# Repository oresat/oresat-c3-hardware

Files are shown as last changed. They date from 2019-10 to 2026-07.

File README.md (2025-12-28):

# oresat-c3
## General information
This is the C3 (Command, Communication, and Control) card for OreSat. It acts as the central control point for the entire OreSat project, provides
telemetry to the ground, and receiver commands. It's the "on board computer" (OBC) of the OreSat bus. It has:

- Octavo OSD335x-SM SIP AM335X-based Cortex A8 Microporcessor
- On Semi AX5043-based L Band (1.265 GHz) receiver
- On Semi AX5043-based UHF Band (436.5 MHz) receiver and transmitter with 1W PA.
- Custom radiation tolerant watchdog timer based on the TI TLV1042 comparator.
- 16 GB eMMC flash data storage
- 1 Mbit of FRAM for high reliability state and variable storage
- Supercapacitor-backed up RTC
- Two antenna deployment circuits
- OreSat Power Domain (OPD) control circuitry

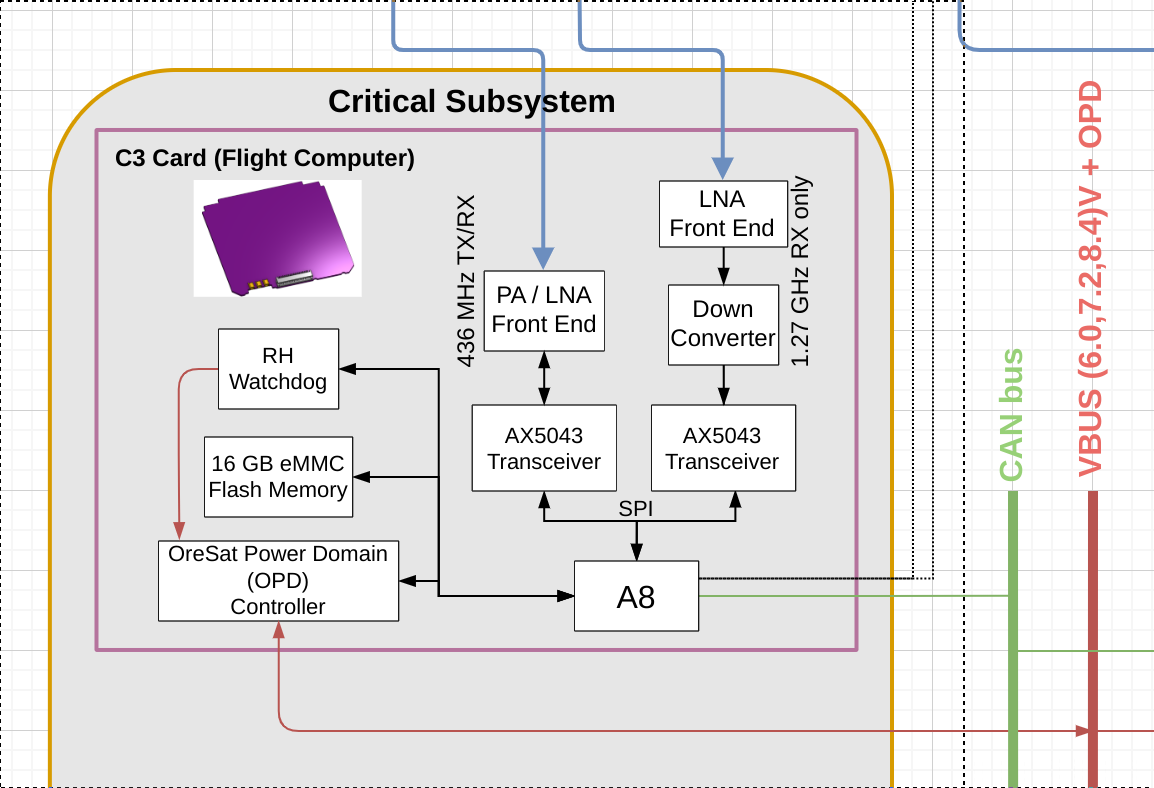
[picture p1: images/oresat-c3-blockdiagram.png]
C3 block digram


Design materials are on Google docs; we'll post links / PDFs soon.

Bill of Materials (BOM) can be found [here](https://docs.google.com/spreadsheets/d/11vG1kWyrAjmbF5QJM-EhXmvQoF6O47japwYlHF802do/edit#gid=1239769296).

## OreSat C3 version 6 (KiCAD)

Fixes for the radio receivers, version 2 backplane pinout, and lots of little tweaks
after our lessons learned on OreSat0. OH, and a COMPLETE REFACTOR since we switched from
the STM32F439 to an Octavo OSD335x-SM and switched from EAGLE to KICAD. Yikes.

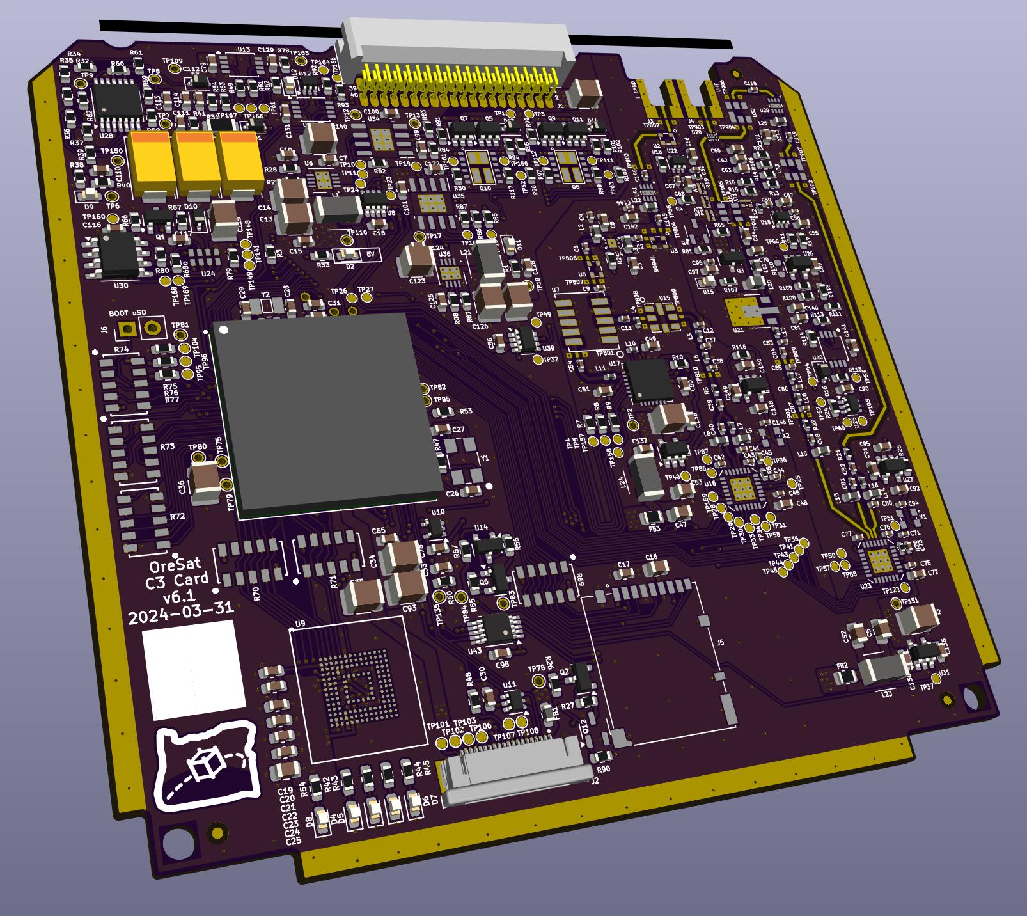
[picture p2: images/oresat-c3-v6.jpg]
C3 version 6 PCBA


### V6 Software

The C3 runs Python code that interacts with the radios, peripherals, and CAN bus. [Here's more information](https://github.com/oresat/oresat-c3-software).

## OreSat C3 version 5 (EAGLE)

C3 V5 flew on Oresat0, Oregon's first satellite! Everything worked great, except for the
radio receivers (L band LNA oscillated, and UHF LNA was turned off in firmware).

### v5 Firmware

The firmware for the C3 card is written in C and runs on top of ChibiOS, a small RTOS.
It is integrated into the [oresat-firmware](https://github.com/oresat/oresat-firmware) repository.
The firmware application for this project is located
[here](https://github.com/oresat/oresat-firmware/tree/c3_capstone/src/f4/app_c3_v1).

## OreSat C3 version 4 (EAGLE)

C3 V4 is our latest version of the C3 card; it's getting ready for flight in 
Q2 2021 in OreSat0. It's got all of the functionality necessary for flight.

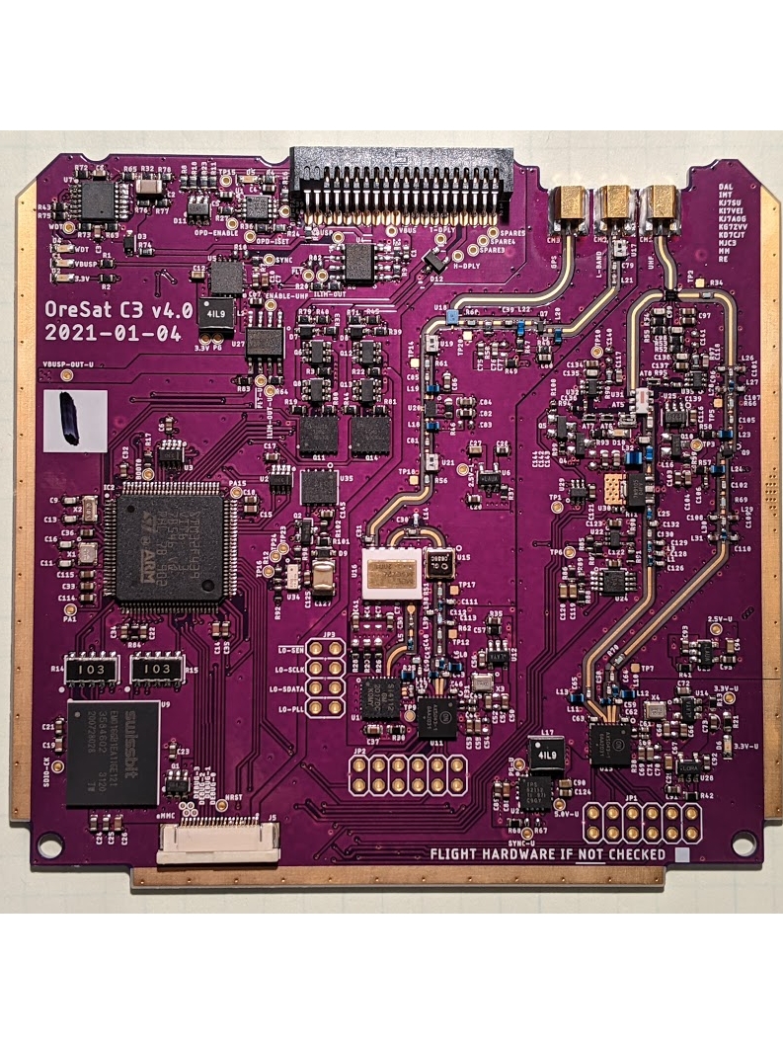
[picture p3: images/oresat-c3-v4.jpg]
C3 version 4 PCBA


## OreSat C3 V3 (2019-2020 ECE Capstone)

The 2018-2019 ECE Capstone brought the card to version 3. It implements an
STM32F446VET6 IC, the full L band receiver with ultistage LNA, and a UHF radio 
with LNA but no PA for transmitting.

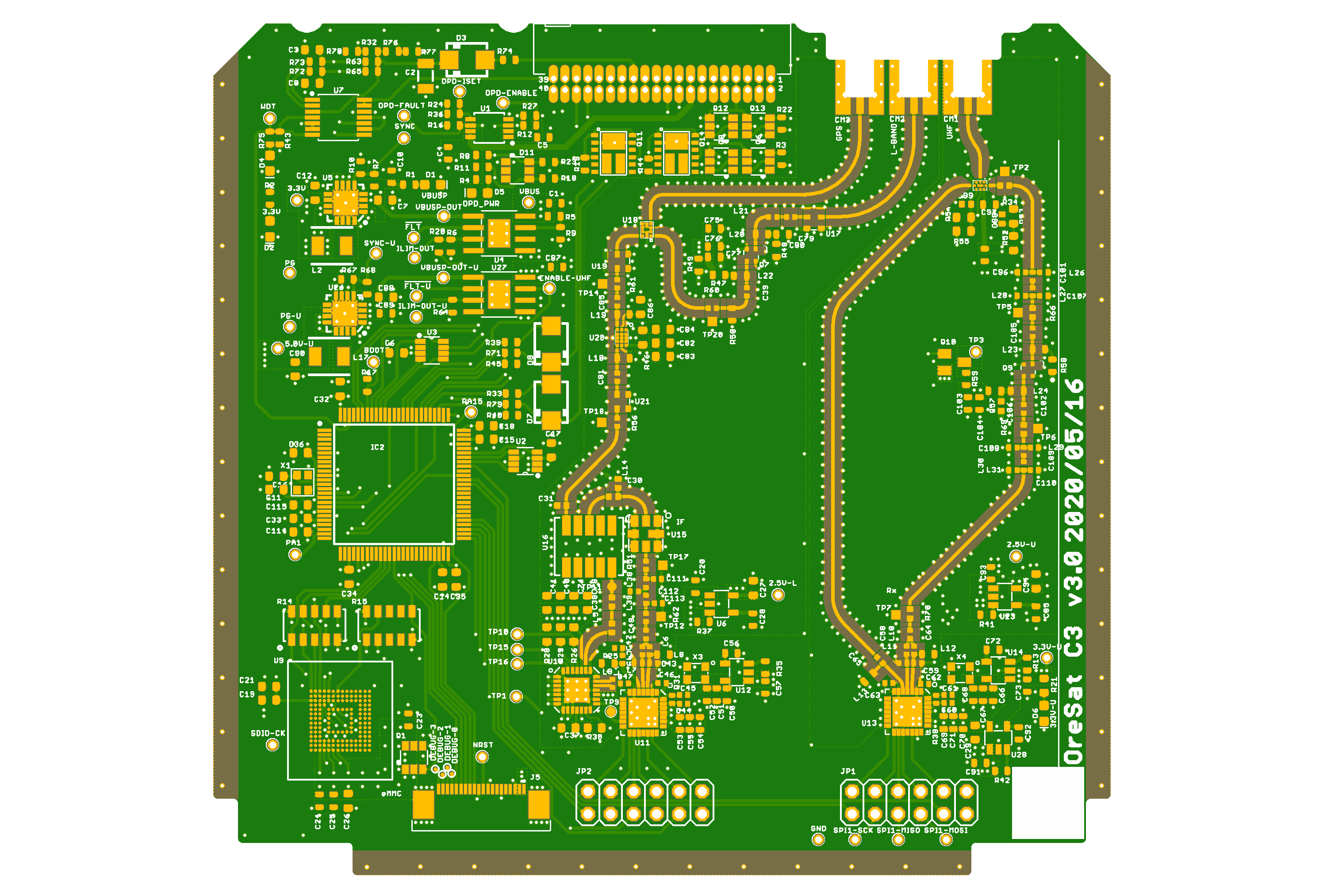
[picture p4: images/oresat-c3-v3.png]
C3 version 3 PCBA


## Breadboard Prototype

Most embedded project starts out as a bunch of development boards strung together;
the C3 is no different! The breadboard prototype for the C3 card implements an
STM32F446RE development board connected to two SPI radios, the OreSat
FlatSat backplane via a CAN transceiver and I2C for the OPD interface,
and a SDIO and SPI connected SD/MMC Card. The breadboard implements
stronger pullups for the I2C lines than the GPIO of the STM32 can
provide. It is currently capable of interfacing with and activating the
OPD connected boards.

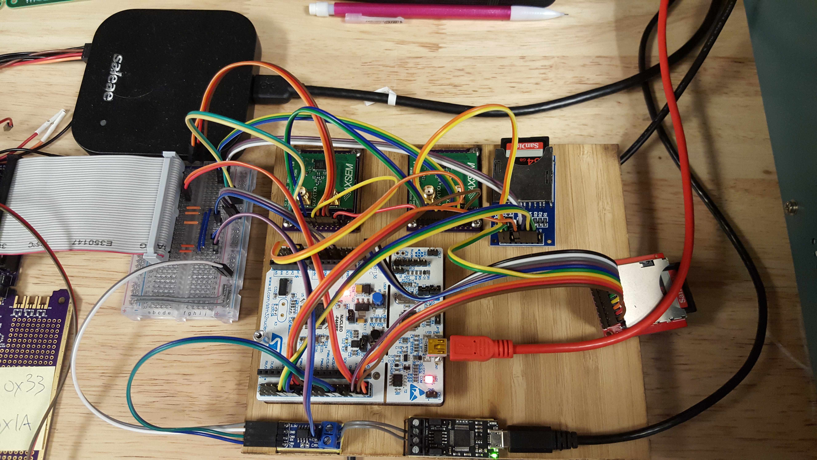
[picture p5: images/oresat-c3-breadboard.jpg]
Breadboard Prototype


## License

All materials in this repo are copyright Portland State Aerospace Society and are licensed under the CERN Open Hardware Licence Version 2 -
Strongly Reciprocal (CERN-OHL-S v2), or any later version. A copy of the license is located in [here](LICENSE.md).

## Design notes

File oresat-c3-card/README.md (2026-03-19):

---
title: "**OreSat C3 Card**"
subtitle: |
  **Fabrication and Assembly Information**\
  For build TIME-STAMP
fontsize: 10pt
geometry:
  - margin=0.5in
toc: true
toc-depth: 2
colorlinks: true
urlcolor: blue
---

\newpage

# About this Board

## Board Description

The C3 ("Command, Control, and Communications") card is the main on-board computer (OBC) / housekeeping unit (HKU) / Command and Data Handling (CDH) subsystem for the open source [OreSat CubeSat system](https://www.oresat.org/). The C3 card:

- Connects to the backplane with a main connector and two RF ports
- Has an L band radio receiver based on the AT86RF215.
- Has a UHF radio transceiver based on the AT86RF215
- Has a radiation tolerant watchdog timer (with a cheap commercial replacement if you're not going to orbit)
- Controls the OreSat Power Domain (OPD), which turns on and off and controls other cards
- Talks to both CAN OreSat CAN busses

## Documentation Links

- C3 hardware Git repository: <https://github.com/oresat/oresat-c3-hardware>
- C3 software Git reposity: <https://github.com/oresat/oresat-c3-software>
- **TODO:** C3 Design Notes + Design Review Notes

## Documentation Files

| Filename | Notes |
| --- | --- |
| README.pdf | This README file |
| PROJECT-NAME-outline.dxf | Board outline (with holes) in DXF format |
| PROJECT-NAME-pcba.step | 3D model of PCBA (with components) |
| PROJECT-NAME-render-bot.jpg | Render of the top of the 3D model |
| PROJECT-NAME-render-bot.jpg | Render of the bottom of the 3D model |
| PROJECT-NAME-schematic.pdf | PDF of board schematics |

## Contact Information

- Website: <https://www.oresat.org/>
- Email: <oresat@pdx.edu>
- Instagram: @pdxaerospace

## Board Renders

Render of the top of the 3D model
Render of the bottom of the 3D model

\newpage

# Printed Circuit Board (PCB) Fabrication Information

## Board Info

- 4 layer board
- Bounding box is 99.8 x 94.6 mm (3.93 x 3.72 in)
- Board thickness is 1.59 mm (0.063 inch)
- **Important:** See Materials and Stack Up sections below

## Board Requirements

- Design Rules
    - Minimum Trace / Space design rules
       - Outer layers: 0.127 mm (5.0 mil) / 0.127 mm (5.0 mil)
       - Inner layers: 0.127 mm (5.0 mil) / 0.127 mm (5.0 mil)
    - Outer dimension router tolerance: +/- 0.254 mm (10.0 mil)
    - Hole placement tolerance: +/- 0.075 mm (3.0 mil)
    - Inner tab routed slot tolerance: +/- 0.254 mm (10.0 mil)
- Drills
   - Drill Positional Tolerance: 0.051 mm (2.0 mil)
   - Drill Size tolerance: +/- 0.064 mm (2.5 mil)
- Plated/Un-plated holes
  - There are 6 un-plated (NPT) holes
  - There are 1477 plated through (PTH) holes
  - PTH minimum diameter: 0.254 mm (10 mil)
  - PTH minimum annulus: 0.102 mm (4 mil) radius
- Outline/Routing
  - Requires a 1.0 mm or smaller diameter routing bit
- Slots
  - There are no slots.
- Cutouts
  - There are no cutouts
- There are 3 fiducials on the top layer.
- Panel tabs ("mouse bites")
   - Card edges must be smooth; no mouse bites or other intrusions into the card outline.
   - If external mouse bites are required, minimize and customer will remove by hand before assembly.
- If not otherwise specified, build to IPC 6012 Class 2 or better.

## Materials

- Controlled impedance
   - The stackup is critical for the performance of high speed signals on this board.
   - As long as the stackup is controlled, the board is not considered controlled impedance.
- Isola FR408HR or material with equivalent Dk.
- Board Surface treatment should be ENIG, althogh immersion Silver is acceptable.
- White silkscreen on top and bottom surface
- Taiyo PSR-4000 or equivalent soldermask on top and bottom, no requirements for color.

## Stack Up

| Layer | Thickness | Notes |
|---|---|---|
| Top Copper | 0.043 mm /  1.7 mil |  Layer 1 foil, 1 oz Cu after plating |
| prepreg | 0.200 mm /  7.9 mil |  Prepreg - Isola FR408HR 2113 |
| Layer 2 | 0.018 mm /  0.7 mil |  Layer 2 foil, 0.5 oz Cu |
| Core | 0.991 mm / 39 mil |  Core Isola FR408HR |
| Layer 3 | 0.018 mm /  0.7 mil |  Layer 3 foil, 0.5 oz Cu |
| prepreg | 0.200 mm /  7.9 mil |  Prepreg - Isola FR408HR 2113 |
| Bottom Copper | 0.043 mm /  1.7 mil |  Layer 4 foil, 1 oz copper after plating |
| **Total Stackup** | **1.588 mm / 62.5 mil** | |

## Array / Panel Information

- Coordinate with Contract Manufacturer (CM) for optimal size of this panel.
- If no feedback from CM, then produce single boards (no panel).

## Fabrication Files

### IPC-2581 File

| Filename | Notes |
| --- | --- |
| PROJECT-NAME-ipc2581.xml | IPC-2581 board information file |

### Legacy PCB Files

| Filename | Notes |
| ---| --- |
| PROJECT-NAME-Edge_Cuts.gbr | RS274X file for the dimension (outline) layer |
| PROJECT-NAME-F_Silkscreen.gbr | RS274X file for the top silkscreen |
| PROJECT-NAME-F_Mask.gbr | RS274X file for the top soldermask |
| PROJECT-NAME-F_Cu.gbr | RS274X file for the top copper layer |
| PROJECT-NAME-In1_Cu.gbr | RS274X file for the layer 2 copper |
| PROJECT-NAME-In2_Cu.gbr | RS274X file for the layer 3 copper |
| PROJECT-NAME-B_Cu.gbr | RS274X file for the bottom copper layer |
| PROJECT-NAME-B_Mask.gbr | RS274X file for the bottom soldermask |
| PROJECT-NAME-B_Silkscreen.gbr | RS274X file for the bottom silkscreen |
| PROJECT-NAME-NPTH.drl | Excellon file for non-plated through holes |
| PROJECT-NAME-PTH.drl | Excellon file for plated through holes | 

\newpage

# Printed Circuit Board Assembly (PCBA) Information

## Assembly Info

- All components are on the top side of the board.
- This PCBA is mostly surface mount (SMT) with a few (THT) components.

## Assembly Requirements

- Assemble to IPC Class 2 or better
- Bake components that are not moisture sealed to appropriate levels as required.
- Solder paste MUST be leaded.
- Aqueous flux and wash strongly preferred.
   - Clean to NASA Standard "Visibly Clean (VC)": No particles or residues are visible to the naked eye.
- No conformal coating.
- Ship in antistatic protective bag

## Component Specific Assembly Information

- SMPM connectors (J3, J4) should be hand-added (there is no solder paste for their footprints).
- U1 and U28 are extremely expensive ($75 and $150 ea, respectively).
- U15 and U21 are EOL and will be supplied in cut tape form.

## Assembly Files

### IPC-2581 File

| Filename | Notes |
| --- | --- |
| PROJECT-NAME-ipc2581.xml | IPC-2581 board information file |

### Bill of Materials (BOM)

| Filename | Description |
| --- | --- |
| PROJECT-NAME-bom.csv | BOM in Comma Separated Variable format |

### Solder Paste Stencils

| Filename | Notes |
| --- | --- |
| PROJECT-NAME-B_Paste.gbr | RS274X file for top/front solder paste stencil |
| PROJECT-NAME-F_Paste.gbr | RS274X file for bottom/back solder paste stencil |

### Mounting/Placement Location

| Filename | Description |
| --- | --- |
| PROJECT-NAME-3u.pos | Pick and place locations for components |

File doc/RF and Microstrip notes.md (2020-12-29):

We use OSH Park 4 layer PCB. 50 ohm line on this is 0.38 mm, as we determined by calculation and by measurement.

Decided to move RF net clearance to 0.75 mm which is ~ 4x the dielectric thickness of 0.17 mm. Better than minimum of 3 and worse than the 5 some people say.

The 0.75 mm clearance means that the total RF "width" of the strip and pulled back ground plane is 0.75 * 2 + 0.38 mm = 1.88 mm.

The TSTOP on the RF traces is 1.6 wide, which protects the ground copper with 0.18 mm of coverage on both sides.

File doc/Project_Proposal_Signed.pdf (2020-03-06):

# OreSat Command, Control, and Communication (C3) Card: Project Requirements and Plan

A 2019-2020 ECE capstone project sponsored by the Portland State Aerospace Society

Mikhail Mayers, Robin Ekeya, Marcus Chalona, Miles Simpson, Ian Taylor

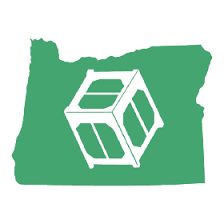
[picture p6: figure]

## Table of Contents

Executive Summary | 3
Project motivation | 3
Product Design Specification | 4
Concept of operations | 4
Stakeholders | 4
Requirements | 5
Design Specifications | 5
Deliverables | 6
Initial Product Design | 7
Oresat C3 Board: Level 0 | 8
Oresat C3 Board: Level 1 | 9
Verification Plans | 11
Project Management Plan | 11
Timeline, with milestones | 11
Budget and Resources | 11
Team and development process | 11

### Executive Summary

Our project’s goal is to deliver a flight ready Command, Control, and Communication (C3) card for OreSat. OreSat (http://cubesat.org/) is Oregon's first satellite. It is an open source 2U CubeSat (https://en.wikipedia.org/wiki/CubeSat) being developed by the Portland State Aerospace Society (PSAS) with a target hand off date to NASA in winter 2021. The C3 card is the "system controller" for the satellite, it oversees the critical, attitude determination/control and mission subsystems.

The C3 card has the radios that link the CubeSat to the mission control on the ground. Once the CubeSat is released from the ISS, the C3 will be responsible for broadcasting a radio beacon so that the ground station can make initial contact and uniquely identify it in space. The C3 is also the heart of OreSat’s radiation tolerance having the single rad-hard part in the satellite.

### Project motivation

OreSat has a modular card-cage system that holds up to 20 cards. On these cards are: the critical subsystems (solar modules, batteries, and telemetry and telecommand radio systems), the attitude determination and control subsystems (IMU, GPS, Star Tracker, Reaction Wheels and Magnetorquers), and finally the mission subsystems (OreSat Live and the Cirrus Flux Camera). The C3 card ties all of these cards together into a functional satellite.

One of the challenges with developing a flight ready CubeSat is the harsh operating environment presented by space. Besides the stresses of vibration and extreme temperatures, ionizing radiation can cause CMOS devices to latch up. OreSat aims to be radiation tolerant while minimizing the use of expensive rad-hard parts. The C3 card makes this possible by retaining the ability to individually power cycle each card in the satellite thereby recovering the malfunctioning card from a single event latch up. The rad-hard watch dog on the C3 power cycles the whole satellite in the event of a latch-up on the MCU.

The C3 Card has redundant radios operating on two bands. The L-Band radio functions as a receiver only and enables the ground station to turn off the transmit/receive UHF radio in case it is stuck transmitting. This is necessary in order to comply with ITU regulations. Besides being the communications backbone, the C3 has onboard eMMC memory which serves as a buffer for mission and telemetry data in transit to and from the ground. The C3 also communicates with the critical and mission subsystems through two separate CAN buses and in this way it forms a common data hub for the whole satellite.

### Product Design Specification

Concept of operations

This project aims to produce a central controller for OreSat. As mentioned above in the project motivation it is the key component that ties upto 20 distinct cards into an operational satellite. It does this by providing the following services:
- Serves as the main point of contact between the cards on the CubeSat with the ground substation
- Provides radiation tolerance to the other OreSat cards by monitoring them and resetting them through OreSat Power Domain (OPD)
- Is itself radiation tolerant since it has a rad-hard watchdog to reset the MCU in case of a latchup
- Provides a memory backed conduit for both telemetry and mission data data between the satellite subsystems and the ground

The final project will deliver a main controller card for the OreSat project. As such it will be used in a CubeSat that will be released from the ISS into orbit. While the proximate client is PSAS since the whole project is open source, other teams can take our work and either use it as is for their own CubeSat projects or else modify and remix it as needed.

The C3 card will be used internally by PSAS on the OreSat project, as such all the expertise to integrate it into the project already exists in house. We do aim to provide complete and explicit design documentation as well as SOPs so that the project could be replicated by a suitably equipped team. While the flight version of the card is single use (it will end its life after about a year in the glorious flames of reentry,) a great part of the value of this project will be the delivery of tested and proven designs contained in the open source intellectual property we will generate. This IP will remain the property of PSAS. With this in mind, even if our version of the C3 card is further improved upon prior to being flown, we will have succeeded if we go through the planned iterations culminating in a tested and functional C3 card.

Stakeholders

This project stakeholders include:
- Portland State Aerospace Society
- Portland State University
- Maseeh College of Engineering
- The capstone design team

Requirements
- Must
- Be a fully compliant OreSat card
- Be powered from the OreSat power bus
■ Be self isolating from the OreSat power bus in the event of an overcurrent condition
- Provide power to the OreSat Power Domain (OPD)
■ Be fault tolerant of OPD overcurrent conditions
- Control OPD
- Communicate with the OreSat critical subsystem over a dedicated bus
- Communicate with OreSat mission subsystems over a dedicated bus
- Have an onboard radiation tolerant watchdog to reset OreSat in the event of a hung MCU
- Have a >=8 GB data storage for gathering mission and telemetry data
- Have and run the UHF (70cm) and L band (23cm) AX5043 sub-GHz radio ICs and downconverter for telemetry and telecommand (designs provided by PSAS)
- Be able to power down the transmit radio to guard against a rogue transmitter
- Handle the space environment: vacuum operation, -40 to +100 °C temperature range, and the vibration of launch
- Be Single Event Upset and Single Event Latchup (SEU/SEL) robust
- All intellectual property must be assigned an open source license, software under the GPL v3 and hardware under the CERN OHL v1.2.
- All project design and documentation must be done using git on OreSat's Github pages.

Design Specifications
- OreSat protocard mechanical design
- 1x STM32F446RE MCU
- 2x CAN
- 1x I2C
- 3x SPI (2x if using SDIO)
- 1x SDIO (if not using SPI)
- 3x GPIO for OPD_PWR Circuit Breaker
- Watchdog interface (protocol TBD)
- 2x TCAN330
- 2x AX5043 Radios
- 1x L-Band Rx only
- 1x UHF Band Tx and Rx

- Power supply circuit breaker
- Dedicated Tx radio circuit breaker
- 1x Switching Power Supply for 3.3V
- OPD power supply circuit breaker
- 1x Watchdog
- Firmware based on ChibiOS RTOS
- Implements ECSS CANbus Extension Protocol for CAN interface to sensors
- Implements CCSDS recommended standards for radio interface

Deliverables

- Project proposal
- Weekly Progress Reports
- Final report
- ECE Capstone Poster Session poster
- At least one fully tested and operational C3 board
- Configuration, Software and Firmware, and EAGLE CAD files.
- Committed to the 'oresat-c3' git repository on Github for hardware
- Committed to the 'oresat-firmware' git repository on Github for firmware
- Complete documentation, including:
- Source code
- ECAD
- Background, including research done and theory of operation
- SOPs for operation

Initial Product Design

Taking the C3 practicum as a starting point. We propose to iteratively design, build and test an OreSat C3 board that meets the specifications above. The C3 practicum took the OreSat flat-sat prototype already implemented on a nucleo board and made a working prototype C3 card complying with the OreSat card cage specifications. This proved to be a drop-in replacement for the nucleo prototype. The two AX5043 radio modules were mated to the practicum board as daughter cards. Going forward, the most significant additions to the practicum board are the following:
- The integration of the L band and UHF band radios as designed by another PSAS member into the C3 card. (Currently these are a series of separate RF modules.)
- The selection and integration of a rad-hard watchdog.
- The selection and integration of an appropriate eMMC module to replace the SD card from the practicum.
- The design and implementation of a TVS circuit for the OPD I²C data lines.

Of these the biggest risks lie in the first. We are taking delivery of a mostly complete radio system. With the exception of two blocks, the individual modules have been built and tested to meet OreSat’s requirements. Since however the radio system comprises both digital and RF components, migrating the system to a single board from its current modular form will change its operating characteristics. Moreover the practicum board layout will have to be reconfigured to make space for this new circuitry as well as to support the implementation of segregated RF power and ground. Beyond this a transmit power amplifier with attendant power monitoring and Tx time-out-timer logic has to be design finalized, built and tested. We do have the benefit of being able to consult with the system designers who are current PSAS members. We also have access to the expertise of the OreSat team and its resources. These considerations make this part of the project feasible in the given time frame.

Of the remaining additions, none presents a real challenge to the combined skills and abilities of the current team. The last major task will be compiling proper documentation as we implement these changes. We plan to progress in an iterative fashion with the goal of producing three tested hardware board revisions with the last fully tested and meeting the given specifications by mid May. We have access to the existing OreSat hardware and software design flow with attendant development, build and test tool chains. These represent a development platform that we can leverage without having to piece it together ourselves.

The goal of the project is an operational, space-ready RF communications module. Here too the expertise of the OreSat team is invaluable. The regulatory environment our product will be operating in has already been researched and de-risked. We are the beneficiaries of this groundwork. Close collaboration between our team members and the appropriate OreSat folks will be necessary to ensure that our designs fit this regulatory framework.

Oresat C3 Board: Level 0

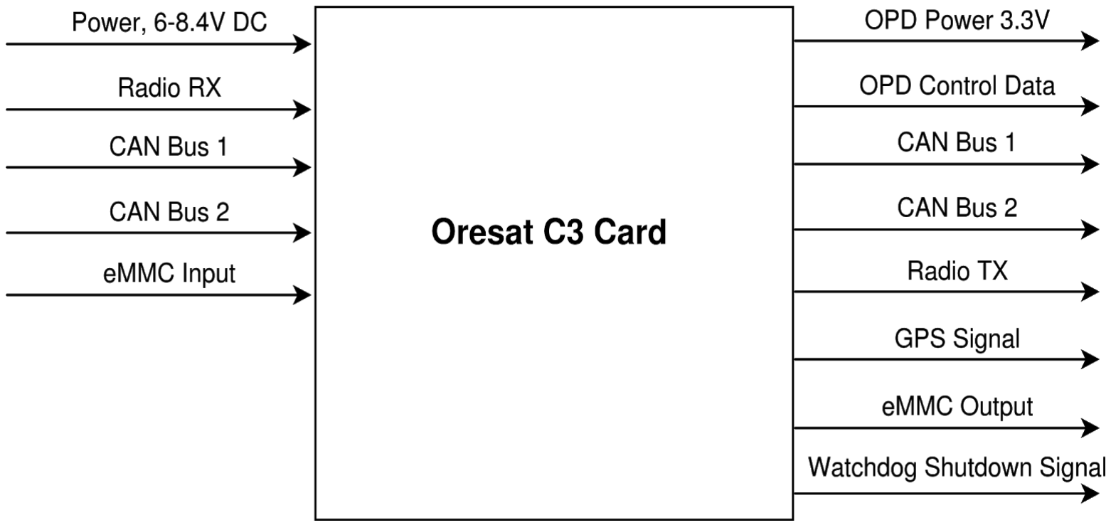
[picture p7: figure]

Module: | Oresat C3 Card
Inputs: | Power (6-8.4 V DC) Radio RX signal (L Band and UHF Band) OPD Control Data (I2C) CAN Bus 1 (critical) CAN Bus 2 (mission) eMMC memory input
Outputs: | OPD Power (3.3 V, 50mA max) OPD Control Data (I2C) CAN Bus 1 (critical) CAN Bus 2 (mission) Radio TX (L Band and UHF Band) eMMC memory output Watchdog Shutdown Signal
Functionality: | Receive 6-8.4 V power from batteries and solar array. Step down voltage to (3.3 V, 300 mA) current limited for internal card usage. Provide power (3.3 V, 50 mA) current limited to OPD. Control Power to each subsystem via OPD Control Data. Communicate with critical subsystems via CAN 1. Communicate with mission subsystems via CAN 2. Receive commands from ground station via Radio RX signal. Cut off UHF PA in case it is stuck on. Transmit mission data via Radio TX signal. Store mission data in eMMC memory. Shutdown entire system power in case of MCU single event latchu-up via Shutdown Signal.

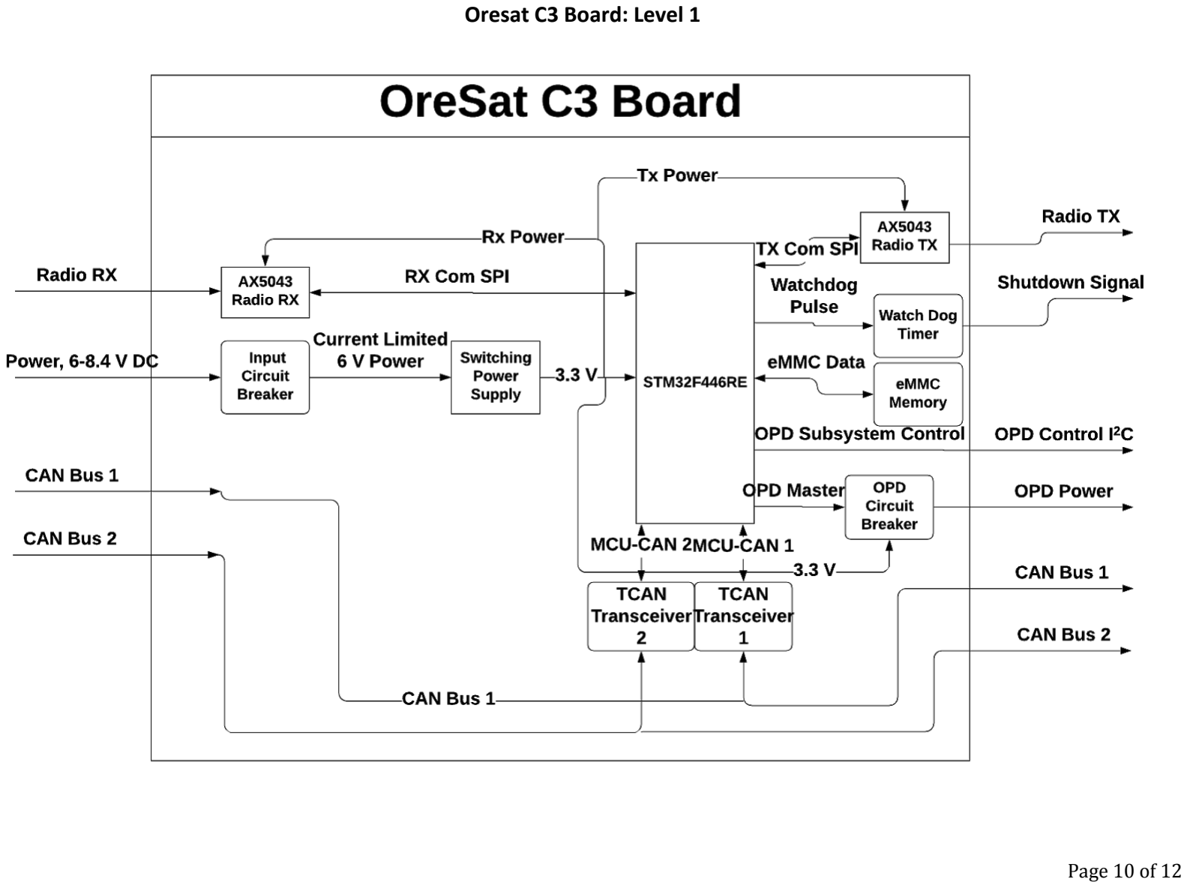
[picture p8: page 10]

Oresat C3 Board: Level 1

Verification Plans

C3 subsystems will be individually tested for functionality where possible as well as interoperability. Please see functional description for functionality to be tested for each system block.

### Project Management Plan

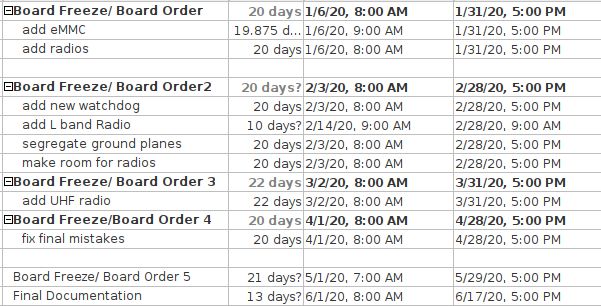
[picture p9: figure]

Timeline, with milestones

Budget and Resources

The resources we will use are as follows:
- The PSAS rocket room
- The EPL
- The Anechoic chamber
- PCB fabrication (Courtesy of OshPark)

- The expertise of the PSAS members spearheading OreSat
- Our personal computers

Our budget for this project is currently set at.

Team and development process

Our team is comprised of five team members:
- Miles Simpson: (Resident OreSat guru and firmware lead)
- OreSat System Engineer
- Firmware Lead
- Mikhail Mayers: (Project Manager and finisher)
- Firmware Helper
- EagleCAD
- Board Stuffing
- Organizer
- Moral Support
- Ian Taylor: (Test and Verification)
- Documentation
- Board Stuffing
- EagleCAD
- Verification/Validation
- Marcus Chalona: (Layout Specialist)
- EagleCAD
- Board Stuffing
- Documentation
- Quality Assurance
- Robin Ekeya: (RF Specialist)
- Analog systems development
- RF systems development
- EagleCAD

Following our industry sponsor’s recommendation, we propose to use a spiral development method. Our plan to generate three board iterations fits this method well.

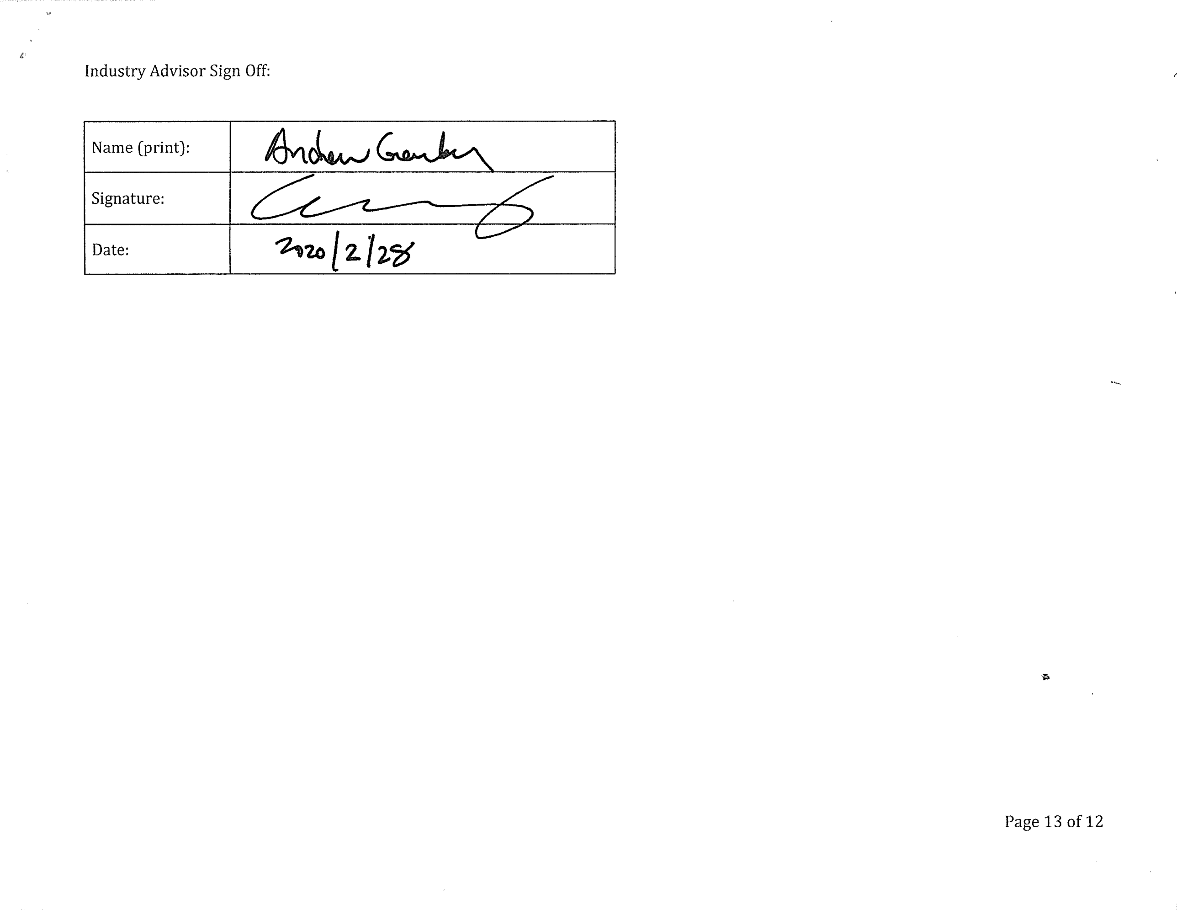
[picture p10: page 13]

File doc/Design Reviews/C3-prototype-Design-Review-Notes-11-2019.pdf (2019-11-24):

# Design Review Notes

## OreSat Command, Control, and Communications Card

## Miles Simpson, Robin Ekeya, Kirk Jungles, Mikhail Mayers

## Version 1.0

10/23/2019

# Department of Electrical and

# Computer Engineering

### Introduction

This document summarizes the notes taken during our two design review meetings. Our first meeting was with Andrew Greenberg on Sunday 11/17/2019 and our second meeting was with Team 11 on Tuesday 11/19/2019. Scribbled notes, which would be largely unintelligible to the untrained eye, were initially jotted down during the design reviews, then after the meetings, our team convened to elucidate the findings of the design reviews and make a list of actions for us to take moving forward. The resulting actions, and therefore the conclusions of the design reviews and notes, are summarized in the following section.

### Design Review Notes/Conclusions

Breakouts Sheet 1:
- JP5 or JP6 need removed
- More test points should be added throughout the board
- Add jumper from AX5043 to ORESAT bus card
- Mark test points on radio breakout pins
- Change net names on radio headers to match names on MCU

Power Sheet 2:
- Provide proper name to CB_IC net
- Move resistor, ground and testpoint from pin 6 of circuit breaker IC to pin 7(!FLT->ILIM)
- Set undervoltage lockout to 5V(Adjust pin 3 voltage divider resistor values)
- Make text note of lockout undervoltage value(5V)
- Make text note of current limit(302 mA)
- Route CB_I_OUT to analog pin on MCU to monitor switch output current
- Add 2.5 V LDO for radio daughter boards*

*May not be necessary. Await further instructions.
Not necessary.

OPD Sheet 3:
- Make OPD power on LED a separate branch on schematic
- Rename !OPD_ON/OFF net to !OPD_ENABLE
- Add Pull up resistor to pin 3 on U1(!ON)
- Add pull up resistor to pin 6 on U1(!fault)
- Make a note on schematic that current limit is set to 50 mA by resistor on pin 5 (SET)
- Add pull up resistors to OPD_I2C lines tying them to OPD_PWR not 3.3V net

MCU Sheet 4:
- Put a note on USART2_RX indicating internal pull up resistor to 3.3V

- Double check that NRST does not require an external pull up tp 3.3V
- Move watchdog LED and resistor near the actual watchdog IC on both schematic and board layout
- Add more capacitors for the unused power pins there are atleast 6 power pins. This is clearer on the board layout
- Route OPD_I_SET to an analog pin on the MCU PB10 is a digital input
- Route CB_I_OUT, U4 pin 7, to an analog input on the MCU
- Add test points to unused GPIO as is practical
- Add a 1uF cap to VDD on SD Card
- Add a 10k pull up to MMC_PWR
- Add a bypass cap on 3.3V Watchdog power
- Add Diode-RC circuit to Watchdog Power as per Andrew’s recommendation
- Add a testpoint to WDT net on watchdog timer
- Set delay times to 3s and 3s(1,0,0)

ERC:
- Change VIN and VOUT pins to power on the MAX892 symbol U1
- Change VIN and VOUT pins to power on the TPS2596 Symbol U4
- Remove OPD_CB_RESET net. It is unused. (PBD 2 on U7)
- Add useful name to U7

Board Layout:
- Route all 3.3V power to layer 15. This is the power plane.
- Check SD Card placement. It can't go past the line on the TSTOP layer indicating where the card is clamped into the CubeSAT backplane.
- Draw in the radio daughter board physical outline. Make sure it does not encroach into any headers.
- Fix angles on the JTAG traces
- Change all signal traces to 0.2 mm
- Make vias uniform
- Route VBUS and VBUSP to layer 15
- Add more stitching throughout board

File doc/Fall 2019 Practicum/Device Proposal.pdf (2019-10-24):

For our practicum, we developed three unique project ideas that have the potential to fulfill all requirements of the practicum. The stated highest level requirements of the practicum project are that it must have a sensor, a controller, and an actuator. We considered a bike-cadence regulating device, an exercise oriented personal lighting system, and a Command, Communication, and Control (C3) board for OreSat. After much deliberation, we decided we would pursue the development of the C3 board for our practicum.

The first project idea was a device that would be installed on a bicycle and would monitor the user's pedal strokes and provide feedback to the user to help him or her maintain cadence, thereby resulting in a maximally efficient bike ride. The device would have an inertial measurement unit (sensor) attached to one of the pedals, which would report the rate of motion to an ATmega32U4 microcontroller (controller) that would be attached to the bike frame. The microcontroller would calculate the average rate of pedaling over the last 100 pedal strokes and determine if the current rate of pedaling is greater than, less than, or equal to the average rate of pedaling. If the current rate was too fast or too slow, it would transmit a signal via a wired connection to illuminate a corresponding number of red or green pixels(respectively) on an RGB LED matrix (actuator) attached to the bicycle's handlebar. The number of lights illuminated would be proportional to the difference between the current pedal rate and the average rate, thereby indicating to the rider whether they should be slowing down or speeding up, and to what extent they should be doing either.

The second project idea was for an exercise oriented personal lighting system. This is a system with neo-pixels or similar individually addressable RGB leds (actuator) that would be mounted on a vest or backpack cover. The leds would be arranged in grid would allow them to be used as a rudimentary display. If used in cyclist mode for example, the system would display a pulsating caution sign. An accelerometer (sensor) mounted on the signing arm would feed into the controller which would decode the following hand signals: stop, right, left, and neutral. Depending on which hand signal was indicated, the vest would display the appropriate pulsating sign: a stop signal, a right arrow, a left arrow, or a caution sign. The system would also have a button to turn the whole system on or off (sensor). If used in night runner mode, the leds would display a caution symbol that would pulsate in a delayed cadence to the runner’s gait sensed by the accelerometer. The system's ATmega32U4 microcontroller board (controller) and battery would be housed in an exercise armband with female 3.5 mm stereo terminals for wires leading to the LED matrix and the accelerometer. Ideally the whole system would run on rechargeable LiPo batteries and would include a charger daughter board to enable battery recharging via a 5 volt mini USB plug.

The third project idea was for a C3 board for OreSat. This board would integrate several different sensors and actuators involved in the OreSat project together and act as the controlling subsystem for OreSat. In the case of the Practicum, this will be a slightly simplified system that integrates together the basic radio interface (actuator/sensor) for communicating data, an STM32 microcontroller with storage that manages the satellite (controller), and several sensors that collect system health data from the satellite via a CAN bus interface (sensors). In addition, the satellite has several subsystems that can be powered on and commanded to perform various operations (actuators). The specific goals we would be focusing on for this practicum will be receiving a command via radio to activate a subsystem (like a sensor), actuating power control circuits to power on the specified subsystem, which will in turn provide its system health data back to the controller (such as temperature and power supply sensor data), and then ultimately relay this data (via actuating the radio interface) down to a receiving station.

In the end, we decided that the C3 board would be our best choice for this practicum. It fulfills all of the requirements of the practicum, it will be of great service to OreSat if we begin contributing to the group through this practicum, and it has the potential to develop into a capstone project that we can work on for the remainder of the school year. We're all very excited to begin working on our project and being part of the greater OreSat team.

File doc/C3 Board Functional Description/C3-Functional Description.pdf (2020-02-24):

# C3 Board Functional Description

Rev 2.0

## Miles Simpson, Robin Ekeya, Marcus Chalona, Mikhail Mayers, Ian Taylor

01/15/2020

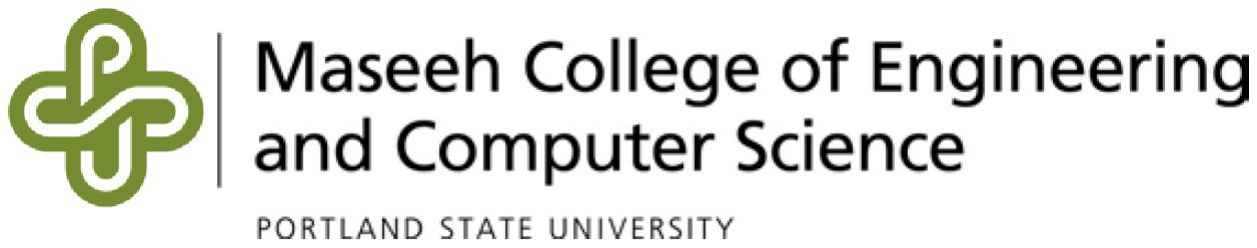
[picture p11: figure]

### Table of Contents

OreSat C3 Board: Level 0 | 2
Oresat C3 Board: Level 1 | 3
AX5043 Radio RX: Level 1 | 4
AX5043 Radio TX: Level 1 | 5
Surge Protector: Level 1 | 6
Circuit Breaker: Level 1 | 7
Radio Soft Switch: Level 1 | 8
TCAN Transceiver: Level 1 | 9
Watchdog Timer: Level 1 | 10
STM32 Microcontroller: Level 1 | 11

### OreSat C3 Board: Level 0

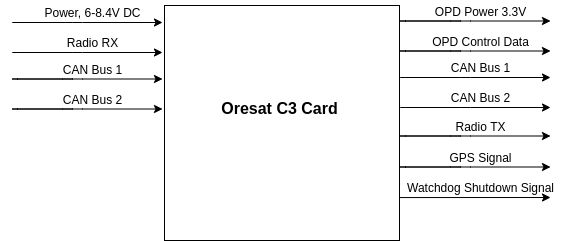
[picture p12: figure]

Module: | Oresat C3 Card
Inputs: | Power (6-8.4 V DC) Radio RX signal(L Band and UHF Band) CAN Bus 1 CAN Bus 2 eMMC Input GPS Signal
Outputs: | Output Power (3.3 V, 200mA max) OPD Control Data (I2C) CAN Bus 1 CAN Bus 2 Radio TX(L Band and UHF Band) eMMC Output Shutdown Signal GPS Signal
Functionality: | Receive 6-8.4 V power from solar array and batteries. Receive commands from ground station via Radio RX signal. Step down power to 3.3 V current limited power supply for OPD subsystem. Control Power to each subsystem via OPD Control Data. Communicate with critical mission subsystems via CAN 1. Communicate with mission subsystems via CAN 2. Transmit mission data via Radio TX signal. Shutdown power to transmit power amplifier in case of a rogue transmitter. Store mission data in eMMC. Shutdown entire system power in case of MCU single event latchup via Shutdown Signal.

Things to Test: 1. Power (TP9 VBUS) from solar array is in the range of 6-8.4V
2. Step down power (TP17 3.3V) is 3.3V ± 0.5V
3. When Watchdog Shutdown Signal (active low) then Fill in blank

### Oresat C3 Board: Level 1

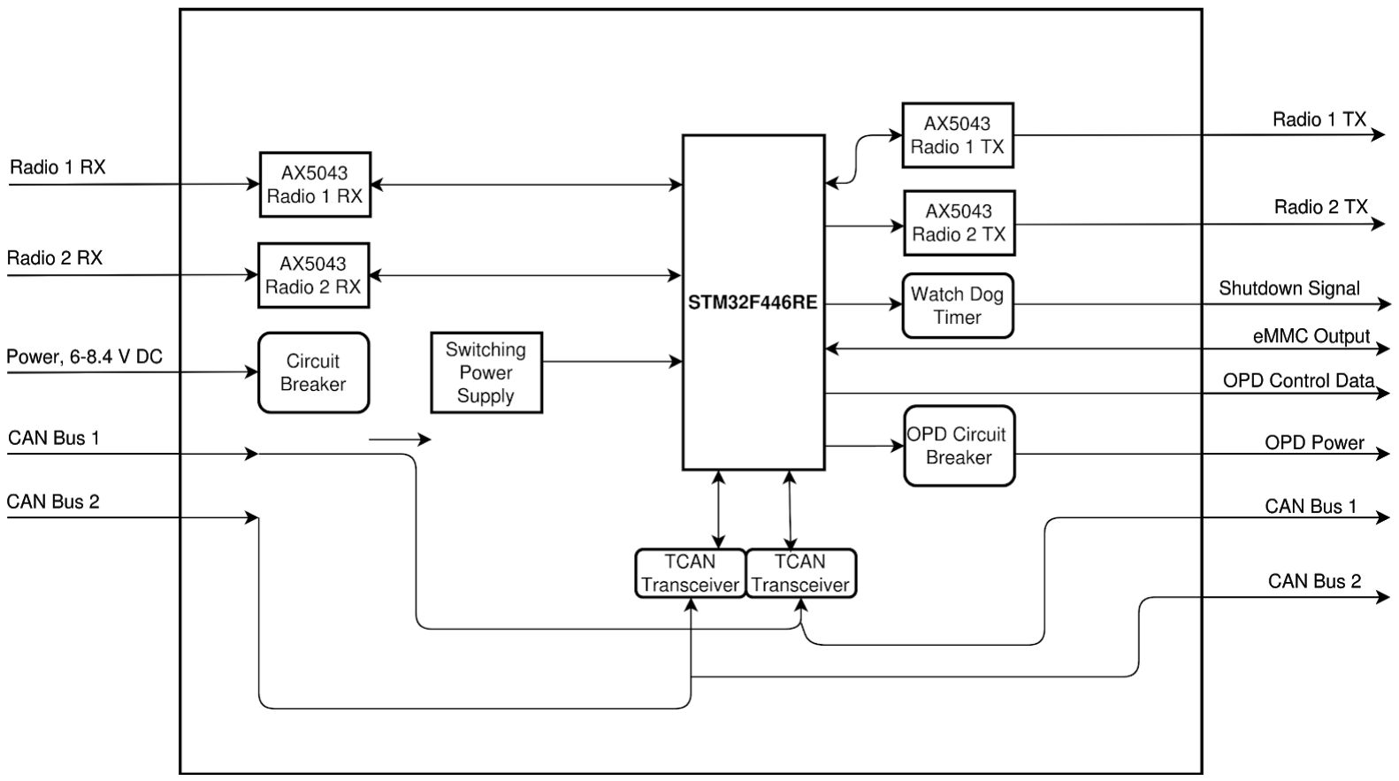
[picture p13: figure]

### AX5043 Radio RX: Level 1

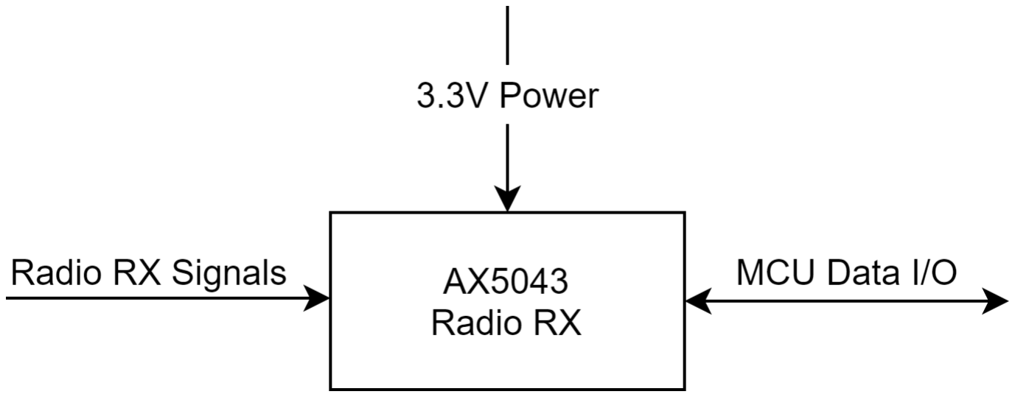
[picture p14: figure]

Module: | AX5043 Radio RX
Inputs: | Radio RX Signals(L Band, UHF Band) Microcontroller Data 3.3 V Power
Outputs: | Microcontroller Data
Functionality: | Receive L Band and UHF signals from ground station. Convert analog RF signals into SPI output for Microcontroller. Receive SPI data from Microcontroller. Gives ground station commands to microcontroller.
Things to Test: | 1. Analog RF to SPI output. 2. Receive SPI data from MCU. 3. 3.3V power in.

### AX5043 Radio TX: Level 1

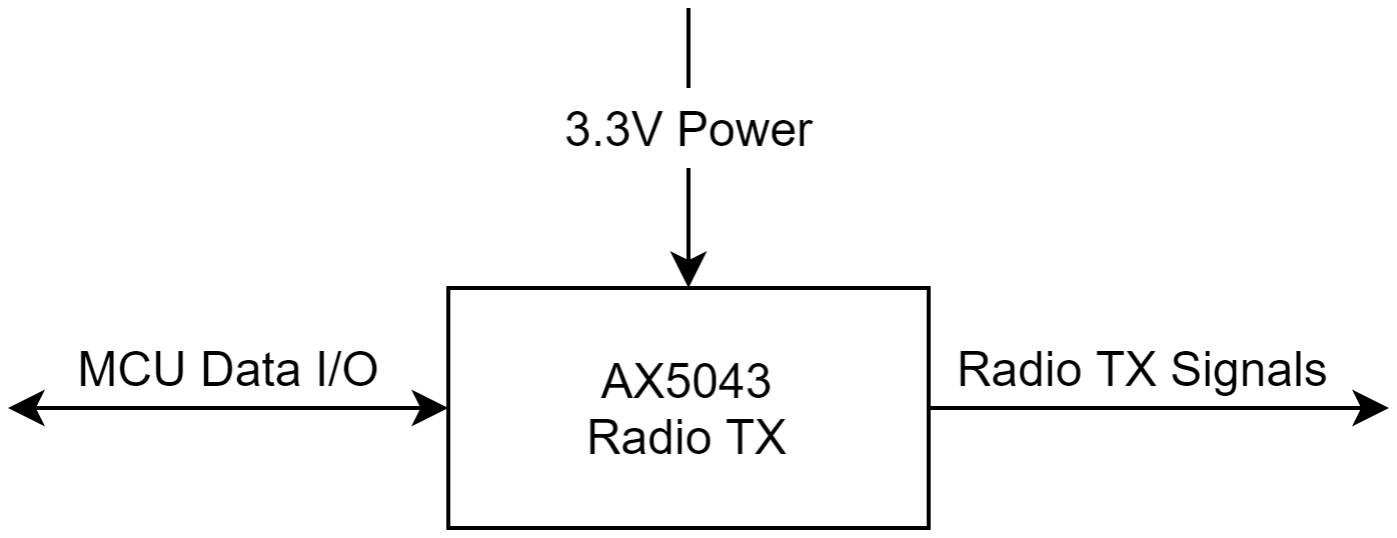
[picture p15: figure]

Module: | AX5043 Radio TX
Inputs: | Microcontroller Data 3.3 V Power
Outputs: | Radio TX Signals( L Band, UHF Band) Microcontroller Data
Functionality: | Receive SPI data from Microcontroller. Transmit system health and mission data to ground stations(L Band, UHF band)
Things to Test: | 1. Analog RF to SPI output. 2. Receive SPI data from MCU. 3. 3.3V Power in.

### Surge Protector: Level 1

Module: | Surge Protector
Inputs: | Radio TX Signals, EMI
Outputs: | Radio TX Signals
Functionality: | Limits Voltage/Current from exceeding the AX5043 IC’s maximum input voltage of 5.5 V. Protects the AX5043 from voltages induced by EMI.
Things to Test: | 1. Input voltage limited to 5.5V. 2. Signal integrity (Look at signal on input vs output)

### Circuit Breaker: Level 1

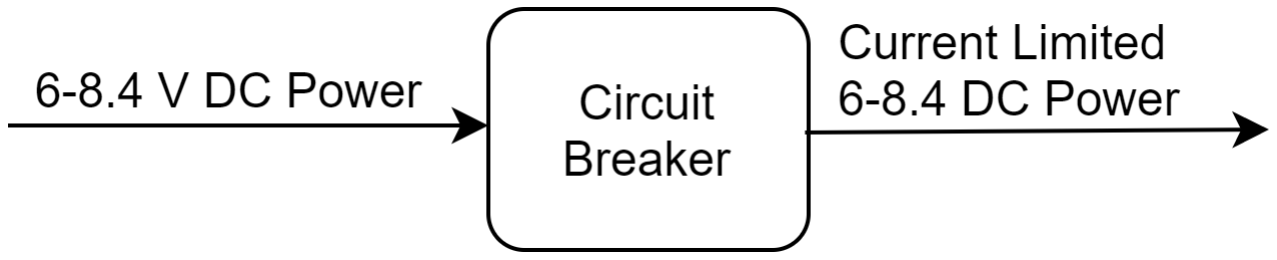
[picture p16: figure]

Module: | Circuit Breaker
Inputs: | 6-8.4 V DC Power
Outputs: | Current Limited 6-8.4 V DC Power
Functionality: | Limit current to protect downstream systems from overcurrent damage. Break circuit if current threshold is reached.
Things to Test: | 1. Input is 6-8.4V 2. Output has limited current.

### Switching Power Supply: Level 1

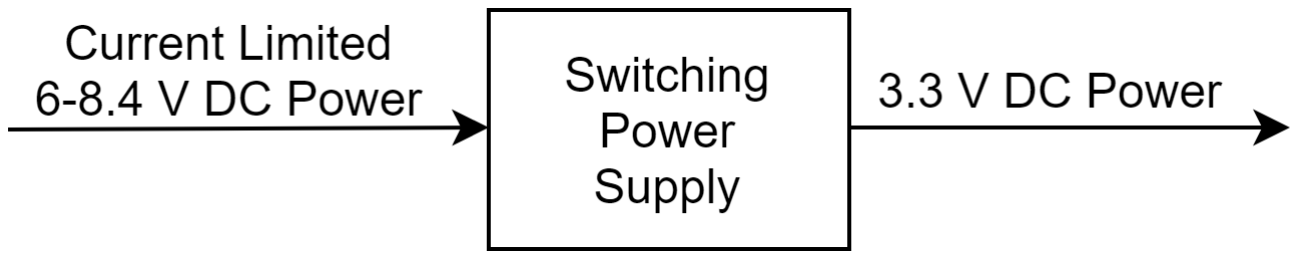
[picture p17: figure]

Module: | Switching Power Supply
Inputs: | Current Limited 6 - 8.4 V DC Power
Outputs: | 3.3 V DC Power
Functionality: | Step down current-limited power supply from 6-8.4 V DC down to 3.3 V DC for use by all subsystems.
Things to Test: | 1. Input is between 6-8.4 V DC. 2. Output is regulated to 3.3 V DC.

### Radio Soft Switch: Level 1

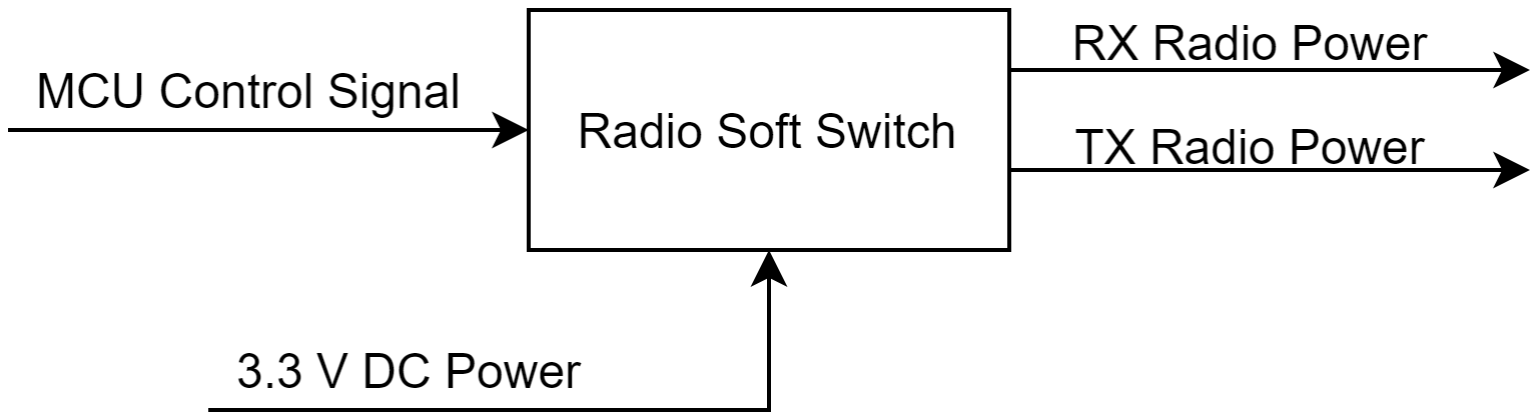
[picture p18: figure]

Module: | Radio Soft Switch
Inputs: | Microcontroller Control Signal 3.3 V DC Power
Outputs: | RX Radio Power (3.3 V DC) TX Radio Power(3.3 V DC)
Functionality: | Receives control signal from microcontroller, determines whether or not to provide power to RX Radio or TX Radio individually.
Things to Test: | 1. 3.3V DC input. 2. Output of Soft Switch based on MCU Control Signal Input.

### TCAN Transceiver: Level 1

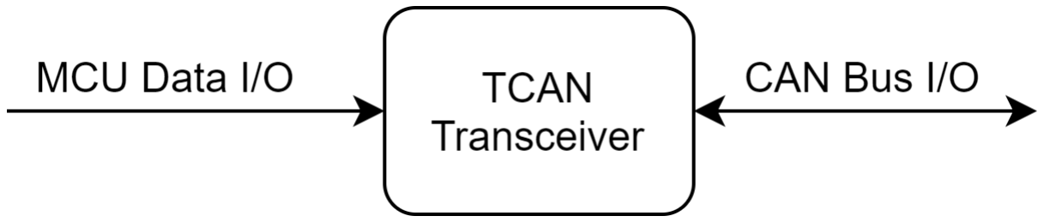
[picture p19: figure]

Module: | TCAN Transceiver
Inputs: | Microcontroller Data CAN Bus Data
Outputs: | Microcontroller Data CAN Bus Data
Functionality: | Receives data from microcontroller, sends down CAN bus. Receives data from CAN bus, sends to microcontroller.
Things to Test: | 1. MCU data on input. 2. I/O on CAN Bus.

### Watchdog Timer: Level 1

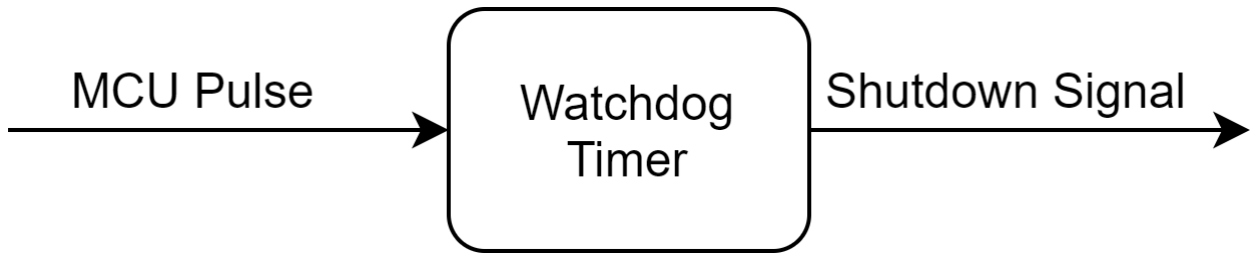
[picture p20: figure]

Module: | Watchdog Timer
Inputs: | Microcontroller Pulse Signal
Outputs: | Shutdown Signal
Functionality: | Receives pulse in regular timed interval from microcontroller indicating system is in good health. Enables shutdown signal if pulse not received, thereby shutting down power to entire Oresat system and resetting.
Things to Test: | 1. MCU Pulse on input. 2. Output Low for reset signal on output.

### STM32 Microcontroller: Level 1

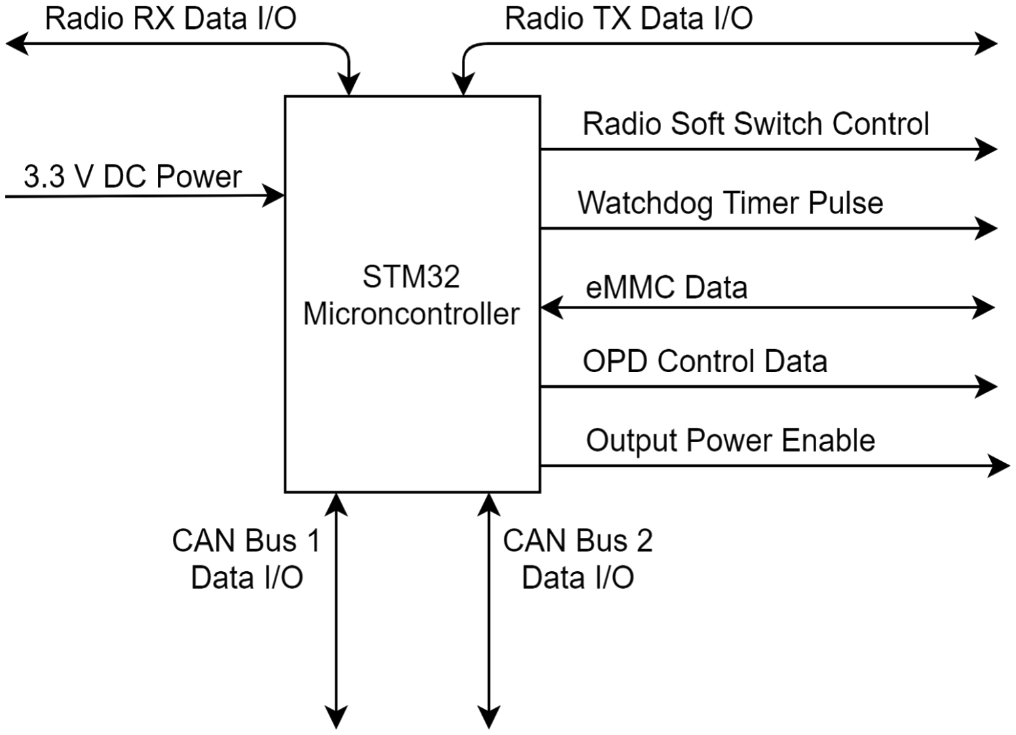
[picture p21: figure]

Module: | STM32 Microcontroller
Inputs: | 3.3 V DC Power CAN Bus 1 Data CAN Bus 2 Data Radio RX Data Radio TX Data eMMC Interface
Outputs: | Radio RX Data Radio TX Data Radio Soft Switch Control Watchdog Timer Pulse eMMC Interface OPD Control Data Output Power CAN Bus 1 CAN Bus 2

Functionality: | Communicates with all critical subsystems through CAN bus 1. Communicates with all mission subsystems through CAN bus 2. Controls power for all subsystems through OPD Control Data line. Reads and writes memory to and from eMMC. Kicks watchdog to indicate system health. Controls power to Radio TX and RX. Receives commands from ground station through Radio RX line. Transmits mission and system health information through Radio TX line.

Things to Test:

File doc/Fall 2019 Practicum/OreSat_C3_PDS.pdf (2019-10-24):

# Product Design Specifications

## OreSat Command, Control, and Communications Card

## Miles Simpson, Robin Ekeya, Kirk Jungles, Mikhail Mayers

## Version 1.0

10/23/2019

# Department of Electrical and

# Computer Engineering

# Portland State University

# Table of Contents

Table of Contents | 1
Executive Summary / Concept of Operations | 2
Marketing Analysis | 2
Requirements | 3
System Architecture | 3
Block Diagram | 4
Design Specifications | 4

# Executive Summary / Concept of Operations

OreSat is an open-source cubesat project that is currently developing Oregon’s first satellite to be launched into space. Our product is the command, control and communications (C3) module for OreSat’s cubesat. It integrates several different sensors and actuators involved in the top level control of the OreSat project. As such, it has the responsibility of controlling the power and data flow to and from various subsystems in the satellite. For the practicum, we are developing a simplified C3 system that integrates the following: a basic radio interface for communicating with the CubeSat, a microcontroller with storage that manages the satellite, several sensors that collect system health data from the rest of the satellite via a CAN bus interface, and a power domain for monitoring and individually power-cycling each connected subsystem.

This practicum project will be used by the OreSat project to demonstrate the control of the rest of the satellite subsystems by the C3 module and will be an open-source project under the MIT Open Source Initiative License. This device will be used during a balloon flight where it will communicate with a ground station. This project will be used as a basis for the C3 flight module to be used on the launched CubeSat. In the future this will be useful to other groups using the OreSat CubeSat specifications on their own projects.

# Marketing Analysis

Since the final deliverable product is a C3 module that will be used during a balloon flight test conducted by OreSat, we regard OreSat as our primary customer. Further down the line, when fully developed into the “space-ready” version that will be used in the actual OreSat CubeSat, this product may serve as a platform for future science missions and the growing CubeSat market. This will extend our potential customer base to include all scientists, engineers, and space hobbyists who would seek to take advantage of the many opportunities for research that have been made available with the advent of CubeSats.

Our product will provide a set of unique advantages over other CubeSats: it will be well-documented with respect to other open source CubeSat projects, it will be radiation-tolerant with minimal use of radiation-hardened components, and have a modular design allowing for variation in the system into which the design is integrated (with some small adjustments). Our product is not to be assessed in terms of selling price, as it is an open-source project developed with the betterment of humanity in mind, but its monetary benefit could instead be quantified in terms of the savings that its users may accrue. Our preliminary estimate of cost based on our Bill of Materials places our total expense at around $300, while similar COTS products are available online for $4,000-$10,000. Surely, our product will be highly coveted in the cubesat market when it is complete.

# Requirements

- Must conform to OreSat card cage specifications
- Must be able to be powered from OreSat power bus
- Must be self-isolating in case of overcurrent condition
- Must be able to provide power to OreSat Power Domain
- Must be fault tolerant of OreSat Power Domain overcurrent conditions
- Must be capable of interfacing with OreSat Power Domain
- Must be capable of interfacing with OreSat critical subsystems
- Should be capable of interfacing with OreSat mission subsystems separate from critical subsystems
- Must provide communications interface with ground stations
- Must provide system health status to ground stations
- Must receive commands from ground stations
- Must provide non-volatile data storage
- Must be able to reset in case of radiation induced single event latch-up of the C3 card

# System Architecture

The mechanical design of this project conforms to the OreSat card cage specifications with regards to dimensions and connectors. This project will have at its core a 32 bit ARM MCU capable of interfacing with all subsystems local to the card as well as all subsystems connected through the OreSat Backplane. VBUS power (6-8.4V) is provided via the backplane, which must pass through a self resetting circuit breaker before being regulated via an SPS to provide 3.3V for use on the card. This card must also provide, through a controllable circuit breaker, power to the OreSat Power Domain (OPD) subsystem via the OPD_PWR connection. It must also be capable of interfacing with this subsystem via I2C using the OPD_SDA and OPD_SCL connections in order to control power to all other subsystems connected to the backplane. Communications with OreSat subsystems are facilitated by two CAN buses provided via the backplane. One CAN bus (CAN1) is used for critical subsystems and must be fully functional, while another (CAN2) is used for mission subsystems and should be able to be used independently of CAN1. In order to communicate with ground stations, the card must provide two radios connected via SPI to the MCU. One radio will be used to broadcast the system health status, while another will receive commands. Non-volatile storage will be provided via a removable SD/MMC card. Finally, the card will incorporate a watchdog that, in case of the MCU hanging, will assert an active low SHUTDOWN signal on the backplane that kills VBUS power to the entire satellite. This is how the satellite is reset in case of an MCU single event latch-up.

## Block Diagram

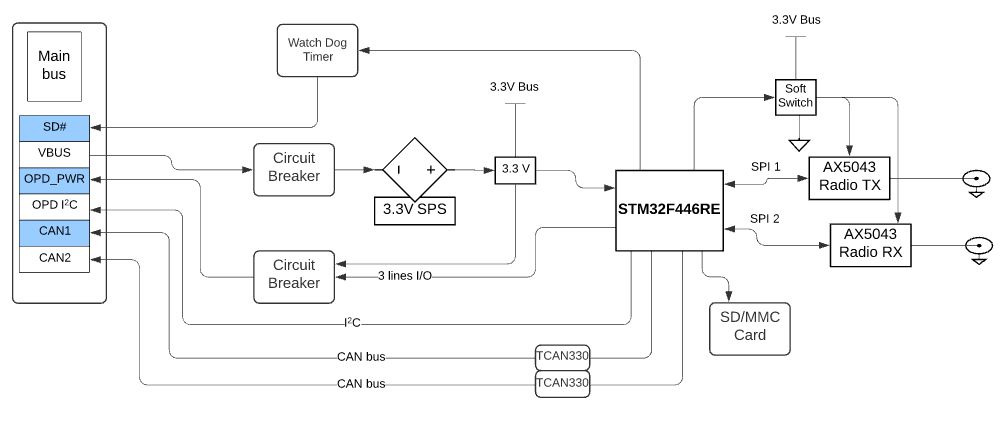
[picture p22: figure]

# Design Specifications

Design specifications were developed after careful consideration of time, budget, current skillset of team, and extant constraints imposed by our predecessors and colleagues on the OreSat team. Those specifications are as follows:
- OreSat protocard mechanical design
- 1x STM32F446RE MCU (processor)
- 2x CAN
- 1x I2C
- 3x SPI (2x if using SDIO)
- 1x SDIO (if not using SPI)
- 3x GPIO for OPD_PWR Circuit Breaker
- Watchdog interface (protocol TBD)
- 2x TCAN330 (sensor/actuator)
- 2x AX5043 Radios (sensor/actuator)
- Power supply circuit breaker
- 1x Switching Power Supply for 3.3V
- OPD power supply circuit breaker (actuator)
- 1x Watchdog (sensor/actuator)
- Firmware based on ChibiOS RTOS
- Implements ECSS CANbus Extension Protocol for CAN interface to sensors (sensors)
- Implements CCSDS recommended standards for radio interface

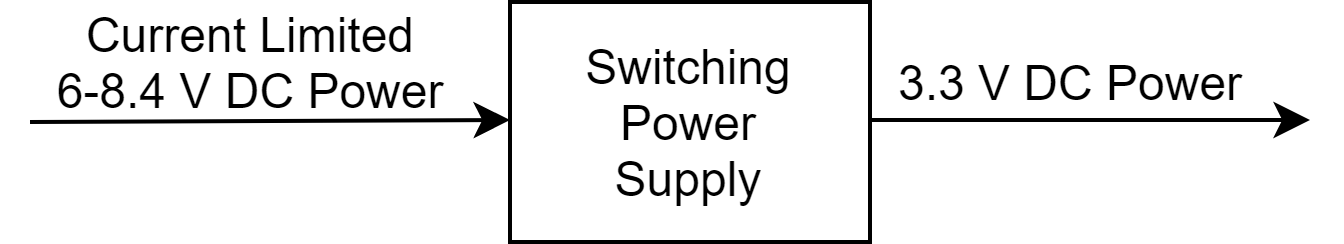
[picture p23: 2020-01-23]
doc/C3 Board Functional Description/Switching Power Supply_ Level 1.png

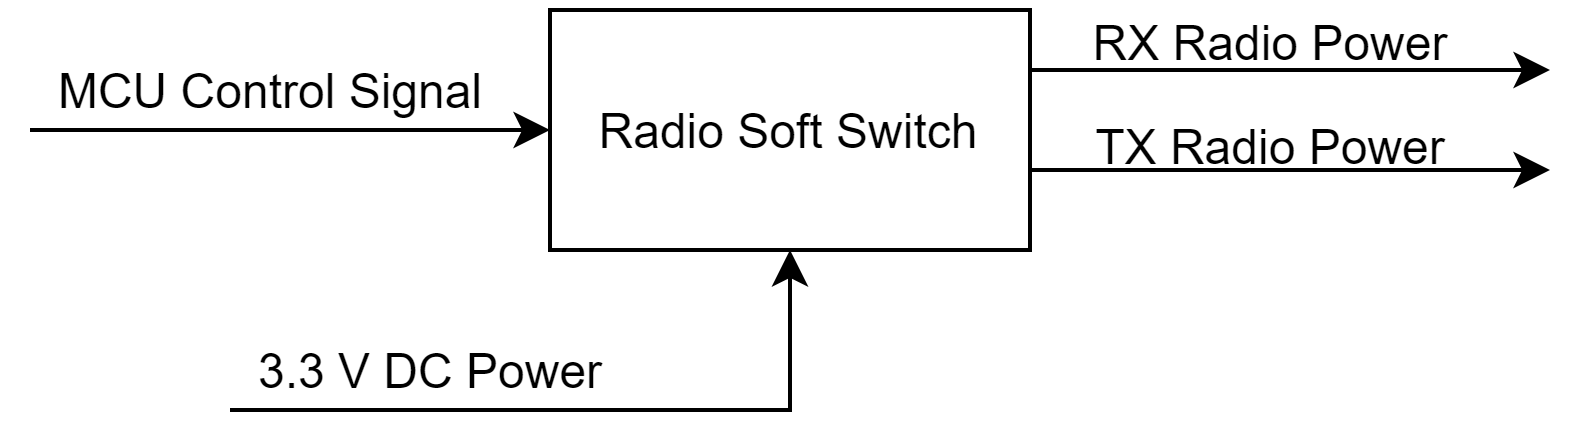
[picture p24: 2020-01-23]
doc/C3 Board Functional Description/Radio Soft Switch_ Level 1.png

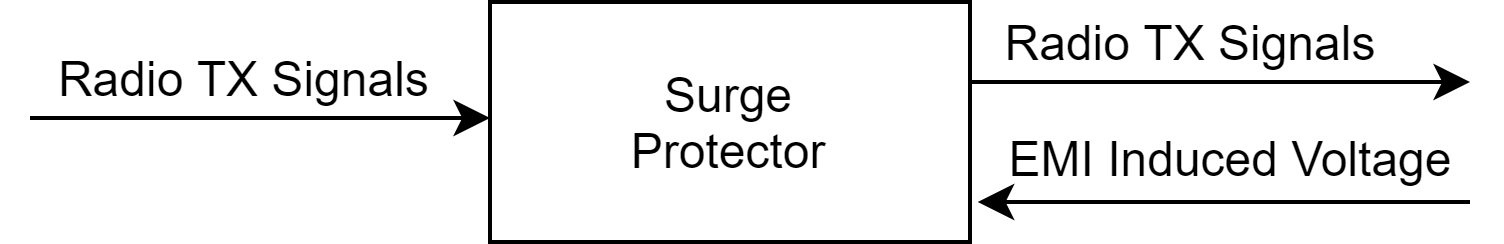
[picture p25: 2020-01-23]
doc/C3 Board Functional Description/Surge Protector_ Level 1.png

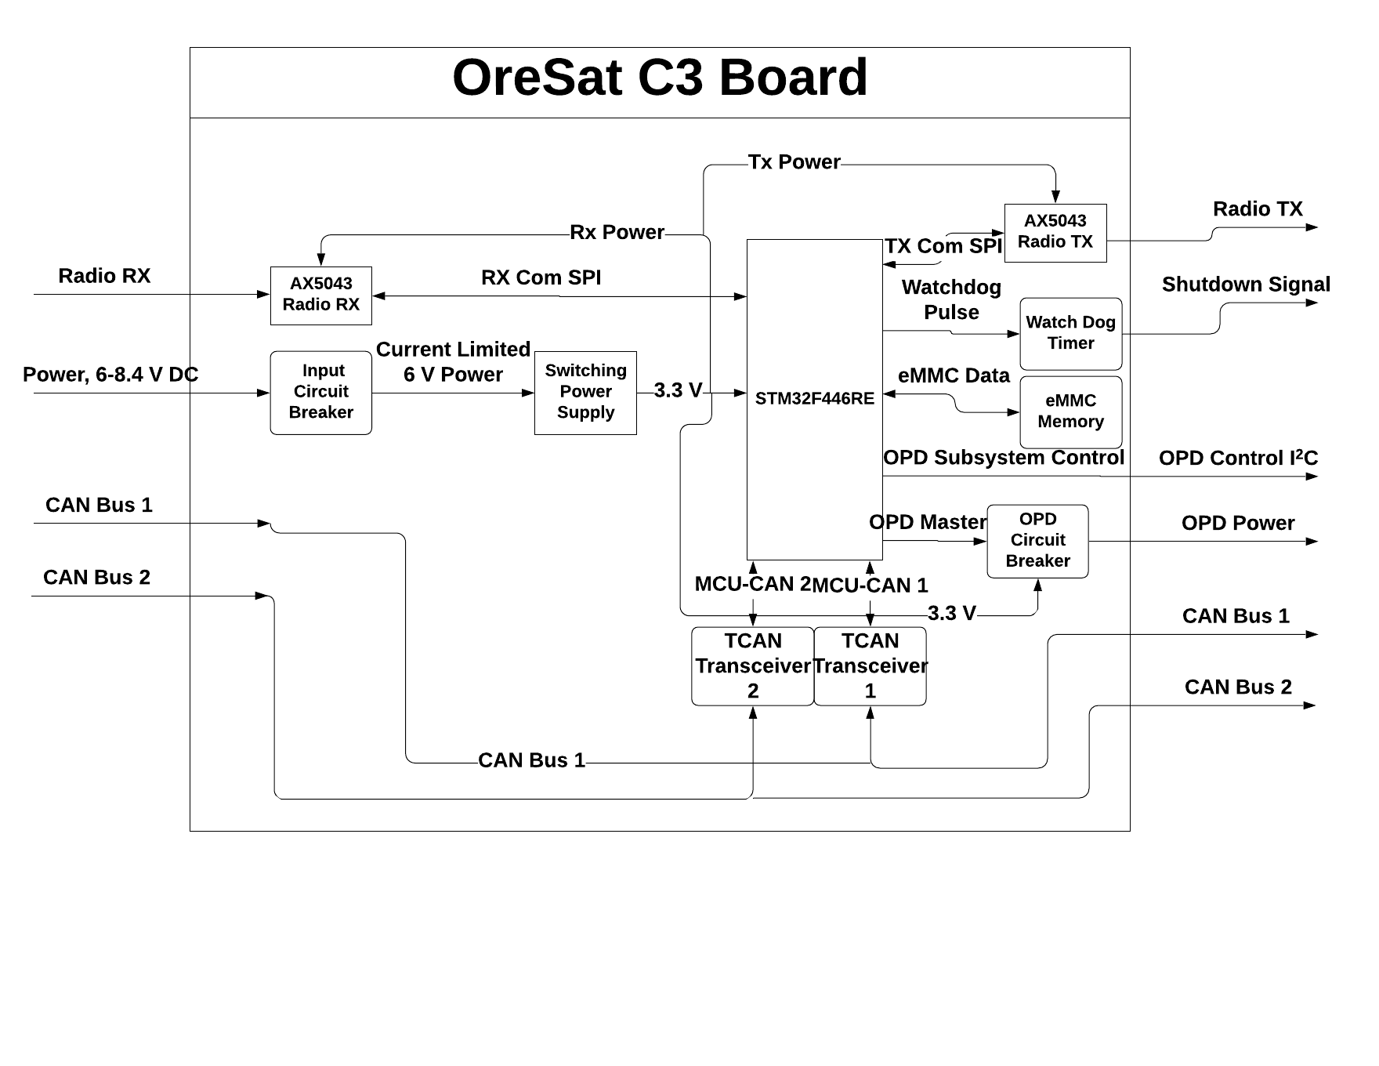
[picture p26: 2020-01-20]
doc/C3 Board Functional Description/C3 Board_ Level 1.png

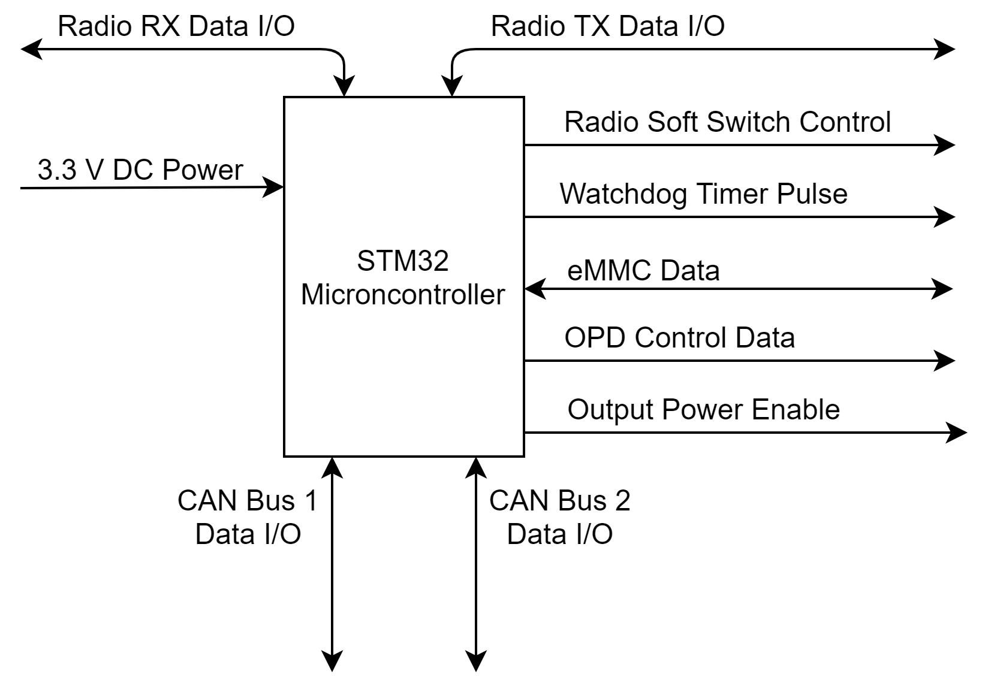
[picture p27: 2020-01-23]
doc/C3 Board Functional Description/STM32 Microcontroller_ Level 1.png

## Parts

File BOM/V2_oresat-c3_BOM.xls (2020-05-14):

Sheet: oresat-c3
Qty | Value | Device | Package | Parts | Description | BOM | DESCRIPTION | DIGI-KEY_PART_NUMBER | DIS | DISCRIPTION | DISTRIBUTOR | DPN | HEIGHT | INVENTORY | LABEL | MANUFACTURER | MANUFACTURER_NAME | MANUFACTURER_PART_NUMBER | MFR | MOUSER_PART_# | MOUSER_PART_NUMBER | MOUSER_PRICE-STOCK | MPN | POPULARITY | PROD_ID | RS_PART_NUMBER | RS_PRICE-STOCK | SPICEPREFIX | VALUE | VDC | VENDOR
1 | STM32F446RE | STM32F446RE | QFP-10X10-64 | U7 |  |  | ARM Microcontrollers - MCU 16/32-BITS MICROS |  |  |  |  |  |  |  |  | STMicroelectronics |  | STM32F446RET6 |  |  | 511-STM32F446RET6
1 | SI4112 | SI4112 | QFN28-5X5-WITH-CENTER-PAD | U10 | RF Synthesizer w/ integrated VCOs (IF OUT) |  | PLL RF Synthesizer, single out, IF |  |  |  | Mouser |  |  |  |  |  | Silicon Labs | SI4112-D-GM |  |  | 634-SI4112-D-GM
1 | MAX892LEUA+T21-0036K-L | MAX892LEUA+T21-0036K-L | 21-0036K-L | U1 | MAX891L / MAX892L |  | Power Switch ICs - Power Distribution Current-Limited, High-Side P-Channel Switches with Thermal Shutdown |  |  |  |  |  |  |  |  | Maxim Integrated |  | MAX892LEUA+T |  |  | 700-MAX892LEUAT |  |  |  |  |  |  |  |  |  | Maxim Integrated Products
2 | PMV45EN2R | PMV45EN2R | SOT23 | Q3, Q5 | Nexperia PMV45EN2R N-channel MOSFET, 5.1 A, 30 V PMV45EN2, 3-Pin SOT-23 |  | Nexperia PMV45EN2R N-channel MOSFET, 5.1 A, 30 V PMV45EN2, 3-Pin SOT-23 |  | Digi-Key |  |  | 1727-2307-1-ND | 1.1mm |  |  |  | Nexperia | PMV45EN2R | Nexperia |  | 771-PMV45EN2R | https://www.mouser.com/Search/Refine.aspx?Keyword=771-PMV45EN2R | PMV45EN2R |  |  | 1364835P | http://uk.rs-online.com/web/p/products/1364835P
1 | Qorvo 856930 | 856930 | 3.8X3.8 | U15 | 457.5 MHz SAW Filter |  | Filter - SAW, 457.5 MHz, 15 MHz |  |  |  | Mouser |  |  |  |  |  | Qorvo | 856930 |  |  | 772-856930
1 | QPC1022 | QPC1022 | QPC1022 | U8 |  |  | RF Switch ICs 5-6000MHz SPDT IL .25dB Iso 39dB |  |  |  |  |  |  |  |  | Qorvo |  | QPC1022TR7 | Qorvo |  | 772-QPC1022TR7 |  | QPC1022
1 | SFEM016GB1EM1TO-A-HG-111-STD | EMMC+RESET-BA | BGA-153(11.5X13)(EMMC-BA) | U9 | eMMC (embedded multi-media card) memory with optional Reset function |  | eMMC 16GB E-MMC MLC EM-20 IND |  |  |  |  |  |  |  |  | Swissbit |  | SFEM016GB1EA1TO-I-GE-111-STD |  |  | 922-500530
1 | LP2985AIM5-1.8_NOPB | LP2985AIM5-1.8_NOPB | SOT-23 | U12 | Micropower 150-mA Low-Noise Ultra-Low-Dropout Regulator in SOT-23 packages |  | Linear Voltage Regulator IC 1 Output 150mA SOT-23-5 | LP2985AIM5-1.8/NOPBCT-ND |  |  | Digikey |  | 1.45mm |  |  |  | Texas Instruments | LP2985AIM5-1.8/NOPB |  |  | 926-2985AIM51.8/NOPB
1 | LP2985AIM5-1.8_NOPB | LP2985AIM5-1.8_NOPB | SOT-23 | U14 | Micropower 150-mA Low-Noise Ultra-Low-Dropout Regulator in SOT-23 packages |  | Micropower 150-mA Low-Noise Ultra-Low-Dropout Regulator in SOT-23 packages | LP2985AIM5-1.8/NOPBCT-ND |  |  |  |  | 1.45mm |  |  |  | Texas Instruments | LP2985AIM5-1.8/NOPB |  |  | 926-2985AIM51.8/NOPB
2 | LP2985AIM5-2.5_NOPB | LP2985AIM5-2.5_NOPB | SOT-23 | U6, U23 | Micropower 150-mA Low-Noise Ultra-Low-Dropout Regulator in SOT-23 packages |  | Micropower 150-mA Low-Noise Ultra-Low-Dropout Regulator in SOT-23 packages |  |  |  |  |  | 1.45mm |  |  |  | Texas Instruments | LP2985AIM5-2.5/NOPB |  |  | 926-2985AIM52.5/NOPB | https://www.mouser.com/Search/Refine.aspx?Keyword=926-2985AIM53.3%2FNOPB
1 | LP2985AIM5-3.3_NOPB | LP2985AIM5-3.3_NOPB | SOT-23 | U28 | Micropower 150-mA Low-Noise Ultra-Low-Dropout Regulator in SOT-23 packages |  | Micropower 150-mA Low-Noise Ultra-Low-Dropout Regulator in SOT-23 packages |  |  |  |  |  | 1.45mm |  |  |  | Texas Instruments | LP2985AIM5-3.3/NOPB |  |  | 926-2985AIM53.3/NOPB | https://www.mouser.com/Search/Refine.aspx?Keyword=926-2985AIM53.3%2FNOPB |  |  |  | 6520033P | http://uk.rs-online.com/web/p/products/6520033P
1 | 2.0n | L-US0402-C-NOSILK | .0402-C-NOSILK | L21 | INDUCTOR, American symbol |  | L - 0402, 2.0n |  |  |  | Mouser |  |  | 1 |  |  |  | 0402CS-2N0XGL |  |  | 994-0402CS-2N0XGLW
1 | 3.9n | L-US0402-C-NOSILK | .0402-C-NOSILK | L4 | INDUCTOR, American symbol |  | L - 0402, 3.9n |  |  |  | Mouser |  |  | 1 |  |  |  | 0402CS-3N9XGL |  |  | 994-0402CS-3N9XGLW
2 | 15.0n | L-US0402-C-NOSILK | .0402-C-NOSILK | L38, L39 | INDUCTOR, American symbol |  | 15nH Unshielded Wirewound Inductor 1.1A 110mOhm 0402 (1005 Metric) | 2035-1081-1-ND |  |  |  |  |  |  |  | Delta Electronics/Components |  | 0402HP-15NXGLW |  |  | 994-0402HP-15NXGLW
2 | 18n | L-US0402-B-NOSILK | .0402-B-NOSILK | L5, L14 | INDUCTOR, American symbol |  | 18nH Unshielded Wirewound Inductor 900mA 120mOhm 0402 (1005 Metric) | 2035-1083-1-ND |  |  |  |  |  |  |  | Delta Electronics/Components |  | 0402HP-18NXGL |  |  | 994-0402HP-18NXGLU
1 | 0.047u | L-US0603-C-NOSILK | .0603-C-NOSILK | L20 | INDUCTOR, American symbol |  | 47nH Unshielded Wirewound Inductor 600mA 280mOhm Max 0603 (1608 Metric) | 490-15832-1-ND |  |  |  |  |  |  |  | Murata Electronics |  | LQW18AS47NG0ZD |  |  | 994-0402HP-47NXGLU
4 | 5.6n | L-US0402-C-NOSILK | .0402-C-NOSILK | L26, L28, L29, L31 | INDUCTOR, American symbol |  | 0402HP Ceramic Chip 5.6 nH 2 % 1.6 A |  |  |  | Mouser |  |  |  |  |  |  | 0402HP-5N6XGLW |  |  | 994-0402HP-5N6XGLW
2 | 68n | L-US0402-C-NOSILK | .0402-C-NOSILK | L27, L30 | INDUCTOR, American symbol |  | L - 0402HPH Ceramic Chip 68 nH 2 % 0.32 A |  |  |  | Mouser |  |  |  |  |  |  | 0402HPH-68NXGLW |  |  | 994-0402HPH-68NXGLW
1 | 22p | C-EU0402-C-NOSILK | .0402-C-NOSILK | C64 | CAPACITOR, European symbol |  | 22pF ±5% 50V Ceramic Capacitor C0G, NP0 0402 (1005 Metric) | 1276-1116-1-ND |  |  |  |  |  |  |  | Samsung Electro-Mechanics |  | CL05C220JB5NNNC |  |  | CL05C220JB5NNNC
15 | 1u | CAP0603-1UF-25VDC | .0603-C-NOSILK-RESISTOR | C1, C4, C5, C10, C20, C23, C24, C25, C28, C87, C89, C91, C92, C93, C95 | 1µF ±10% 25V Ceramic Capacitor X5R 0603 (1608 Metric) |  | 1µF ±10% 25V Ceramic Capacitor X5R 0603 (1608 Metric) | 311-1445-1-ND |  |  |  |  |  |  |  | YAGEO (PHYCOMP) |  | CC0603KRX5R8BB105 |  |  |  |  |  |  |  |  |  |  |  | 25V
12 | 10k | R0603-10K-OHMS | .0603-C-NOSILK-RESISTOR | R7, R8, R9, R11, R16, R17, R20, R24, R27, R44, R45, R68 | 10 kOhms ±1% 0.1W, 1/10W Chip Resistor 0603 (1608 Metric) Moisture Resistant Thick Film |  | 10 kOhms ±1% 0.1W, 1/10W Chip Resistor 0603 (1608 Metric) Moisture Resistant Thick Film | CR0603-FX-1002ELFCT-ND |  |  |  |  |  |  |  | Bourns |  | CR0603-FX-1002ELF
10 | 0.1u | CAP0603-0.1UF | .0603-B-NOSILK-CAP | C2, C3, C6, C8, C9, C13, C17, C21, C22, C119 | 0.1µF ±10% 10V Ceramic Capacitor X5R 0603 (1608 Metric) |  | 0.1µF ±10% 10V Ceramic Capacitor X5R 0603 (1608 Metric) | 478-0603ZD104KAT2ACT-ND |  |  |  |  |  |  |  | AVX |  | 0603ZD104KAT2A |  |  |  |  |  |  |  |  |  |  |  | 10V
7 | 22p | C-EU0402-C-NOSILK | .0402-C-NOSILK | C39, C48, C49, C65, C79, C81, C85 | CAPACITOR, European symbol |  | 22pF ±5% 50V Ceramic Capacitor C0G, NP0 0402 (1005 Metric) | 1276-1116-1-ND |  |  |  |  |  |  |  | Samsung Electro-Mechanics |  | CL05C220JB5NNNC
5 | 100k | R0603-100K-OHMS | .0603-C-NOSILK-RESISTOR | R13, R35, R37, R41, R42 | 100 kOhms ±5% 0.1W, 1/10W Chip Resistor 0603 (1608 Metric) Automotive AEC-Q200 Thick Film |  | 100 kOhms ±1% 0.1W, 1/10W Chip Resistor 0603 (1608 Metric) Automotive AEC-Q200 Thick Film | RMCF0603FT100KCT-ND |  |  |  |  |  |  |  | Stackpole Electronics Inc |  | RMCF0603FT100K
5 | 1u | C-EU0603-C-NOSILK | .0603-C-NOSILK | C57, C73, C75, C100, C103 | CAPACITOR, European symbol |  | 1µF ±10% 25V Ceramic Capacitor X5R 0603 (1608 Metric) | 311-1445-1-ND |  |  |  |  |  |  |  | Yageo |  | CC0603KRX5R8BB105 |  |  |  |  |  |  |  |  |  |  |  | 25V
5 | 22u | CAP0603-22UF | .0603-B-NOSILK-CAP | C12, C27, C29, C90, C94 | 22µF ±20% 10V Ceramic Capacitor X5R 0603 (1608 Metric) |  | 22µF ±20% 10V Ceramic Capacitor X5R 0603 (1608 Metric) | ZRB18AR61A226ME01L-ND |  |  |  |  |  |  |  | Murata Electronics |  | ZRB18AR61A226ME01L |  |  |  |  |  |  |  |  |  |  |  | 10V
4 | 0 | R-US_0402-B-NOSILK | .0402-B-NOSILK | R34, R66, R69, R70 | RESISTOR, American symbol |  | 0 Ohms Jumper 0.063W, 1/16W Chip Resistor 0402 (1005 Metric) Automotive AEC-Q200 Thick Film | RMCF0402ZT0R00CT-ND |  |  |  |  |  |  |  | Stackpole Electronics Inc |  | RMCF0402ZT0R00
4 | 0 | R-US_0402-C-NOSILK | .0402-C-NOSILK | R51, R56, R60, R61 | RESISTOR, American symbol |  | 0 Ohms Jumper 0.063W, 1/16W Chip Resistor 0402 (1005 Metric) Automotive AEC-Q200 Thick Film | RMCF0402ZT0R00CT-ND |  |  | Digikey |  |  | 107 |  | Stackpole Electronics Inc |  | RMCF0402ZT0R00
4 | 10k | R-US_0402-B-NOSILK | .0402-B-NOSILK | R32, R33, R39, R40 | RESISTOR, American symbol |  | 10 kOhms ±1% 0.063W, 1/16W Chip Resistor 0402 (1005 Metric) Moisture Resistant Thick Film | 311-10.0KLRCT-ND |  |  |  |  |  |  |  | Yageo |  | RC0402FR-0710KL
4 | 2.7k | R0603-2.7K-OHMS | .0603-C-NOSILK-RESISTOR | R1, R2, R3, R4 | 2.7 kOhms ±1% 0.1W, 1/10W Chip Resistor 0603 (1608 Metric) Moisture Resistant Thick Film |  | 2.7 kOhms ±1% 0.1W, 1/10W Chip Resistor 0603 (1608 Metric) Moisture Resistant Thick Film | CR0603-FX-2701ELFCT-ND |  |  |  |  |  |  |  | Bourns |  | CR0603-FX-2701ELF
4 | 22n | C-EU0603-C-NOSILK | .0603-C-NOSILK | C50, C53, C66, C69 | CAPACITOR, European symbol |  | 0.022µF ±10% 25V Ceramic Capacitor X7R 0603 (1608 Metric) | 1276-1999-1-ND |  |  |  |  |  |  |  | Samsung Electro-Mechanics |  | CL10B223KA8NNNC
4 | 24p | C-EU0402-C-NOSILK | .0402-C-NOSILK | C96, C107, C108, C110 | CAPACITOR, European symbol |  | 24pF ±5% 50V Ceramic Capacitor C0G, NP0 0402 (1005 Metric) | 1276-1670-1-ND |  |  |  |  |  |  |  | Samsung Electro-Mechanics |  | CL05C240JB5NNNC |  |  |  |  |  |  |  |  |  |  |  | 50V
4 | 4.7u | C-EU0603-C-NOSILK | .0603-C-NOSILK | C52, C55, C68, C71 | CAPACITOR, European symbol |  | 4.7µF ±10% 16V Ceramic Capacitor X5R 0603 (1608 Metric) | 1276-1784-1-ND |  |  |  |  |  |  |  | Samsung Electro-Mechanics |  | CL10A475KO8NNNC
4 | 43n | L-US0402-C-NOSILK | .0402-C-NOSILK | L6, L7, L10, L11 | INDUCTOR, American symbol |  | 43nH Unshielded Wirewound Inductor 515mA 516mOhm Max 0402 (1005 Metric) | 490-15447-1-ND |  |  |  |  |  |  |  | Murata Electronics |  | LQW15AN43NG8ZD
4 | 47k | R-US_0603-B-NOSILK | .0603-B-NOSILK | R26, R28, R29, R30 | RESISTOR, American symbol |  | 47 kOhms ±1% 0.1W, 1/10W Chip Resistor 0603 (1608 Metric) Moisture Resistant Thick Film | 311-47.0KHRCT-ND |  |  |  |  |  |  |  | Yageo |  | RC0603FR-0747KL
4 | 8.2p | C-EU0402-C-NOSILK | .0402-C-NOSILK | C42, C43, C58, C59 | CAPACITOR, European symbol |  | 8.2pF ±0.25pF 50V Ceramic Capacitor C0G, NP0 0402 (1005 Metric) | 1276-1729-1-ND |  |  |  |  |  |  |  | Samsung Electro-Mechanics |  | CL05C8R2CB5NNNC
4 | 82p | C-EU0402-C-NOSILK | .0402-C-NOSILK | C46, C47, C62, C63 | CAPACITOR, European symbol |  | 82pF ±5% 50V Ceramic Capacitor C0G, NP0 0402 (1005 Metric) | 1276-1726-1-ND |  |  |  |  |  |  |  | Samsung Electro-Mechanics |  | CL05C820JB5NNNC
4 | 91n | L-US0603-C-NOSILK | .0603-C-NOSILK | L8, L9, L23, L24 | INDUCTOR, American symbol |  | 91nH Unshielded Wirewound Inductor 520mA 540mOhm Max 0603 (1608 Metric) | 490-15756-1-ND |  |  |  |  |  |  |  | Murata Electronics |  | LQW18AN91NG8ZD
4 | GREEN | LED-GREEN0603 | LED-0603 | D1, D2, D5, D6 | Green SMD LED |  | Green 573nm LED Indication - Discrete 2V 0603 (1608 Metric) | 732-12017-1-ND |  |  |  |  |  |  |  | Würth Elektronik |  | 150060VS55040 |  |  |  |  |  |  |  |  |  |  | GREEN
3 | 0 | R0603-0-OHMS | .0603-C-NOSILK-RESISTOR | R12, R19, R22 | 0 Ohms Jumper 0.1W, 1/10W Chip Resistor 0603 (1608 Metric) Thick Film |  | 0 Ohms Jumper 0.1W, 1/10W Chip Resistor 0603 (1608 Metric) Thick Film | 541-4012-1-ND |  |  |  |  |  |  |  | Vishay Dale |  | CRCW06030000Z0EAC
3 | 10u | CAP0603-10UF-25VDC | .0603-B-NOSILK-CAP | C7, C26, C88 | 10µF ±10% 25V Ceramic Capacitor X5R 0603 (1608 Metric) |  | 10µF ±10% 25V Ceramic Capacitor X5R 0603 (1608 Metric) | 490-18214-1-ND |  |  |  |  |  |  |  | Murata Electronics |  | GRM188R61E106KA73D |  |  |  |  |  |  |  |  |  |  |  | 25V
3 | BP0805A1308 | BP0805A1308 | BP0805 | U17, U19, U21 | Thin Film Bandpass Filter |  | 1.308GHz Frequency Band Pass RF Filter (Radio Frequency) 200MHz Bandwidth 1.2dB 0805 (2012 Metric), 4 PC Pad | 478-12187-1-ND |  |  |  |  |  |  |  |  | AVX Corp | BP0805A1308ASTR
3 | MOSFET-PCH-SOT23-6 | MOSFET-PCH-SOT23-6 | SOT23-6 | Q1, Q2, Q4 | P channel MOSFET in an SOT23-6 |  | P-Channel 30V 4.5A (Ta) 1.8W (Ta) Surface Mount TSOT-26 | DMP3050LVT-7DICT-ND |  |  |  |  |  |  |  | Diodes Incorporated |  | DMP3050LVT-7
2 | 10 | R0603-10-OHMS | .0603-C-NOSILK-RESISTOR | R18, R23 | 10 Ohms ±1% 0.1W, 1/10W Chip Resistor 0603 (1608 Metric) Moisture Resistant Thick Film |  | 10 Ohms ±1% 0.1W, 1/10W Chip Resistor 0603 (1608 Metric) Moisture Resistant Thick Film | CR0603-FX-10R0ELFCT-ND |  |  |  |  |  |  |  | Bourns |  | CR0603-FX-10R0ELF
2 | 27 | R-US_0603-C-NOSILK | .0603-C-NOSILK | R47, R59 | RESISTOR, American symbol |  | 27 Ohms ±1% 0.1W, 1/10W Chip Resistor 0603 (1608 Metric) Automotive AEC-Q200 Thick Film | RMCF0603FT27R0CT-ND |  |  |  |  |  |  |  | Stackpole Electronics Inc |  | RMCF0603FT27R0
2 | 0.047u | C-EU0603-C-NOSILK | .0603-C-NOSILK | C76, C80 | CAPACITOR, European symbol |  | 0.047µF ±10% 50V Ceramic Capacitor X7R 0603 (1608 Metric) | 1276-1063-1-ND |  |  | Digikey |  |  | 92 |  | Samsung Electro-Mechanics |  | CL10B473KB8NNNC |  |  |  |  |  |  |  |  |  |  |  | 50V
2 | 100p | C-EU0402-C-NOSILK | .0402-C-NOSILK | C102, C105 | CAPACITOR, European symbol |  | 1000pF ±5% 50V Ceramic Capacitor C0G, NP0 0402 (1005 Metric) | 1276-1635-1-ND |  |  | Digikey |  |  |  |  | Samsung Electro-Mechanics |  | CL05C102JB5NNNC |  |  |  |  |  |  |  |  |  |  |  | 50V
2 | 10k | EXB-A10P391JC_ARRAY_EXBA-M | ARRAY_EXBA-M | R14, R15 |  |  | 10k Ohm ±5% 62.5mW Power Per Element Bussed Resistor Network/Array ±200ppm/°C 2512 (6432 Metric), Concave, Long Side Terminals | U7103CT-ND |  |  |  |  |  |  |  | Panasonic Electronic Components |  | EXB-A10P103J
2 | 10n | C-EU0603-C-NOSILK | .0603-C-NOSILK | C56, C72 | CAPACITOR, European symbol |  | 10000pF ±5% 25V Ceramic Capacitor C0G, NP0 0603 (1608 Metric) | 1276-2172-1-ND |  |  |  |  |  |  |  | Samsung Electro-Mechanics |  | CL10C103JA8NNNC |  |  |  |  |  |  |  |  |  |  |  | 25V
2 | 18.0p | C-EU0402-C-NOSILK | .0402-C-NOSILK | C111, C113 | CAPACITOR, European symbol |  | 18pF ±5% 50V Ceramic Capacitor C0G, NP0 0402 (1005 Metric) | 1276-1140-1-ND |  |  |  |  |  |  |  | Samsung Electro-Mechanics |  | CL05C180JB5NNNC
2 | 1n | C-EU0402-C-NOSILK | .0402-C-NOSILK | C44, C45 | CAPACITOR, European symbol |  | 1000pF ±5% 50V Ceramic Capacitor C0G, NP0 0402 (1005 Metric) | 1276-1635-1-ND |  |  |  |  |  |  |  | Samsung Electro-Mechanics |  | CL05C102JB5NNNC |  |  |  |  |  |  |  |  |  |  |  | 50V
2 | 1n | C-EU0402-C-NOSILK | .0402-C-NOSILK | C60, C61 | CAPACITOR, European symbol |  | 1000pF ±5% 50V Ceramic Capacitor C0G, NP0 0402 (1005 Metric) | 1276-1635-1-ND |  |  |  |  |  |  |  | Samsung Electro-Mechanics |  | CL05C102JB5NNNC
2 | 1u | C-EU0603-B-NOSILK | .0603-B-NOSILK | C78, C82 | CAPACITOR, European symbol |  | 1µF ±10% 25V Ceramic Capacitor X5R 0603 (1608 Metric) | 311-1445-1-ND |  |  |  |  |  |  |  | Yageo |  | CC0603KRX5R8BB105 |  |  |  |  |  |  |  |  |  |  |  | 25V
2 | 2.0p | C-EU0402-C-NOSILK | .0402-C-NOSILK | C101, C109 | CAPACITOR, European symbol |  | 2pF ±0.25pF 50V Ceramic Capacitor C0G, NP0 0402 (1005 Metric) | 311-1006-2-ND |  |  |  |  |  |  |  | Yageo |  | CC0402CRNPO9BN2R0 |  |  |  |  |  |  |  |  |  |  |  | 50V
2 | 2.2u | CAP0603-2.2UF | .0603-B-NOSILK-CAP | C14, C19 | 2.2µF ±20% 10V Ceramic Capacitor X7R 0603 (1608 Metric) |  | 2.2µF ±20% 10V Ceramic Capacitor X7R 0603 (1608 Metric) | 445-5959-1-ND |  |  |  |  |  |  |  | TDK |  | C1608X7R1A225M080AC |  |  |  |  |  |  |  |  |  |  |  | 10V
2 | 20p | CAP0603-20PF | .0603-B-NOSILK-CAP | C11, C16 | 20pF ±5% 50V Ceramic Capacitor C0G, NP0 0603 (1608 Metric) |  | 20pF ±5% 50V Ceramic Capacitor C0G, NP0 0603 (1608 Metric) | GRM1885C1H200JA01J-ND |  |  |  |  |  |  |  | Murata Electronics |  | GRM1885C1H200JA01J |  |  |  |  |  |  |  |  |  |  |  | 50V
2 | 22n | C-EU0603-B-NOSILK | .0603-B-NOSILK | C37, C41 | CAPACITOR, European symbol |  | 0.022µF ±10% 25V Ceramic Capacitor X7R 0603 (1608 Metric) | 1276-1999-1-ND |  |  |  |  |  |  |  | Samsung Electro-Mechanics |  | CL10B223KA8NNNC
2 | 22n | L-US0603-C-NOSILK | .0603-C-NOSILK | L18, L19 | INDUCTOR, American symbol |  | 27nH Unshielded Wirewound Inductor 440mA 210mOhm Max 0603 (1608 Metric) | 490-6879-1-ND |  |  |  |  |  |  |  | Murata Electronics |  | LQW18AN27NG00D
2 | 3.1k | R0603-3.1K-OHMS | .0603-C-NOSILK-RESISTOR | R6, R64 | 3.1 kOhms ±1% 0.125W, 1/8W Chip Resistor 0603 (1608 Metric) Anti-Sulfur Thin Film |  | 3.1 kOhms ±1% 0.125W, 1/8W Chip Resistor 0603 (1608 Metric) Anti-Sulfur Thin Film | MCT06030C3101FP500-ND |  |  |  |  |  |  |  | Vishay Beyschlag |  | MCT06030C3101FP500
2 | 5.6k | R-US_0603-B-NOSILK | .0603-B-NOSILK | R52, R55 | RESISTOR, American symbol |  | 5.6 kOhms ±1% 0.1W, 1/10W Chip Resistor 0603 (1608 Metric) Automotive AEC-Q200 Thick Film | RMCF0603FT5K60CT-ND |  |  |  |  |  |  |  | Stackpole Electronics Inc |  | RMCF0603FT5K60
2 | 6.8k | R-US_0603-B-NOSILK | .0603-B-NOSILK | R53, R54 | RESISTOR, American symbol |  | 6.8 kOhms ±1% 0.1W, 1/10W Chip Resistor 0603 (1608 Metric) Automotive AEC-Q200 Thick Film | RMCF0603FT6K80CT-ND |  |  |  |  |  |  |  | Stackpole Electronics Inc |  | RMCF0603FT6K80
2 | 6.8u | L-ECS-MPI4040 | ECS-MPI4040 | L2, L17 |  |  | 6.8µH Shielded Inductor 2.4A 91mOhm Nonstandard | XC2337CT-ND |  |  |  |  |  |  |  | ECS Inc. |  | ECS-MPI4040R4-6R8-R
2 | 91n | L-US0603-C-NOSILK | .0603-C-NOSILK | L12, L13 | INDUCTOR, American symbol |  | 91nH Unshielded Wirewound Inductor 520mA 540mOhm Max 0603 (1608 Metric) | 490-15756-1-ND |  |  | Digikey |  |  | 5 |  | Murata Electronics |  | LQW18AN91NG8ZD
2 | TCAN330 | TCAN330 | SOT23-8_TI-DCN | U2, U3 |  |  | 1/1 Transceiver CANbus SOT-23-8 | 296-44211-1-ND |  |  |  |  |  |  |  | Texas Instruments |  | TCAN330GDCNT
2 | U-ONSEMI-AX5043 | U-ONSEMI-AX5043 | QFN28-5X5-WITH-CENTER-PAD | U11, U13 |  |  | IC RF TxRx Only General ISM < 1GHz 27MHz ~ 1.05GHz 28-VFQFN Exposed Pad | AX5043-1-TW30OSCT-ND |  |  |  |  |  |  |  | ON Semiconductor |  | AX5043-1-TW30
1 | 0 | R-US_0402-C-NOSILK | .0402-C-NOSILK | R62 | RESISTOR, American symbol |  | 0 Ohms Jumper 0.063W, 1/16W Chip Resistor 0402 (1005 Metric) Automotive AEC-Q200 Thick Film | RMCF0402ZT0R00CT-ND |  |  |  |  |  |  |  | Stackpole Electronics Inc |  | RMCF0402ZT0R00
1 | 15 | R-US_0603-C-NOSILK | .0603-C-NOSILK | R49 | RESISTOR, American symbol |  | 15 Ohms ±1% 0.1W, 1/10W Chip Resistor 0603 (1608 Metric) Automotive AEC-Q200 Thick Film | RMCF0603FT15R0CT-ND |  |  | Digikey |  |  |  |  | Stackpole Electronics Inc |  | RMCF0603FT15R0
1 | 39 | R-US_0603-C-NOSILK | .0603-C-NOSILK | R57 | RESISTOR, American symbol |  | 39 Ohms ±1% 0.1W, 1/10W Chip Resistor 0603 (1608 Metric) Automotive AEC-Q200 Thick Film | RMCF0603FT39R0CT-ND |  |  |  |  |  |  |  | Stackpole Electronics Inc |  | RMCF0603FT39R0
1 | 50 | R-US_0402-C-NOSILK | .0402-C-NOSILK | R25 | RESISTOR, American symbol |  | 50 Ohms ±0.1% 0.05W, 1/20W Chip Resistor 0402 (1005 Metric) RF, High Frequency Thin Film | FC0402-50BWCT-ND |  |  |  |  |  |  |  | Vishay Thin Film |  | FC0402E50R0BST1
1 | 150 | R-US_0402-C-NOSILK | .0402-C-NOSILK | R38 | RESISTOR, American symbol |  | 150 Ohms ±0.1% 0.063W, 1/16W Chip Resistor 0402 (1005 Metric) Thin Film | YAG4175CT-ND |  |  |  |  |  |  |  | Yageo |  | RT0402BRD07150RL
1 | 150 | R-US_0402-C-NOSILK | .0402-C-NOSILK | R31 | RESISTOR, American symbol |  | 150 Ohms ±0.1% 0.063W, 1/16W Chip Resistor 0402 (1005 Metric) Thin Film | YAG4175CT-ND |  |  | Digikey |  |  |  |  | Yageo |  | RT0402BRD07150RL
1 | 220 | R-US_0603-C-NOSILK | .0603-C-NOSILK | R50 | RESISTOR, American symbol |  | 220 Ohms ±1% 0.1W, 1/10W Chip Resistor 0603 (1608 Metric) Automotive AEC-Q200 Thick Film | RMCF0603FT220RCT-ND |  |  |  |  |  |  |  | Stackpole Electronics Inc |  | RMCF0603FT220R
1 | 0.047u | C-EU0603-B-NOSILK | .0603-B-NOSILK | C86 | CAPACITOR, European symbol |  | 0.047µF ±10% 50V Ceramic Capacitor X7R 0603 (1608 Metric) | 1276-1063-1-ND |  |  |  |  |  |  |  | Samsung Electro-Mechanics |  | CL10B473KB8NNNC |  |  |  |  |  |  |  |  |  |  |  | 50V
1 | 0.047u | C-EU0603-B-NOSILK | .0603-B-NOSILK | C84 | CAPACITOR, European symbol |  | 0.047µF ±10% 50V Ceramic Capacitor X7R 0603 (1608 Metric) | 1276-1063-1-ND |  |  | Digikey |  |  | 92 |  | Samsung Electro-Mechanics |  | CL10B473KB8NNNC |  |  |  |  |  |  |  |  |  |  |  | 50V
1 | 0.047u | C-EU0603-C-NOSILK | .0603-C-NOSILK | C104 | CAPACITOR, European symbol |  | 0.047µF ±10% 50V Ceramic Capacitor X7R 0603 (1608 Metric) | 1276-1063-1-ND |  |  |  |  |  |  |  | Samsung Electro-Mechanics |  | CL10B473KB8NNNC |  |  |  |  |  |  |  |  |  |  |  | 50V
1 | 0.1u | C-EU0603-C-NOSILK | .0603-C-NOSILK | C97 | CAPACITOR, European symbol |  | 0.1µF ±10% 10V Ceramic Capacitor X5R 0603 (1608 Metric) | 478-0603ZD104KAT2ACT-ND |  |  |  |  |  |  |  | AVX |  | 0603ZD104KAT2A
1 | 100p | C-EU0402-B-NOSILK | .0402-B-NOSILK | C98 | CAPACITOR, European symbol |  | 1000pF ±5% 50V Ceramic Capacitor C0G, NP0 0402 (1005 Metric) | 1276-1635-1-ND |  |  |  |  |  |  |  | Samsung Electro-Mechanics |  | CL05C102JB5NNNC |  |  |  |  |  |  |  |  |  |  |  | 50V
1 | 100p | C-EU0402-B-NOSILK | .0402-B-NOSILK | C99 | CAPACITOR, European symbol |  | 1000pF ±5% 50V Ceramic Capacitor C0G, NP0 0402 (1005 Metric) | 1276-1635-1-ND |  |  | Digikey |  |  |  |  | Samsung Electro-Mechanics |  | CL05C102JB5NNNC |  |  |  |  |  |  |  |  |  |  |  | 50V
1 | 10n | L-US0603-C-NOSILK | .0603-C-NOSILK | L22 | INDUCTOR, American symbol |  | 10nH Unshielded Wirewound Inductor 650mA 110mOhm Max 0603 (1608 Metric) | 490-6856-1-ND |  |  |  |  |  |  |  | Murata Electronics |  | LQW18AN10NG00D‎
1 | 12.0p | C-EU0402-C-NOSILK | .0402-C-NOSILK | C112 | CAPACITOR, European symbol |  | 12pF ±5% 50V Ceramic Capacitor C0G, NP0 0402 (1005 Metric) | 1276-1178-1-ND |  |  |  |  |  |  |  | Samsung Electro-Mechanics |  | CL05C120JB5NNNC
1 | 16MHZ-2.5x2mm | CRYSTAL-WITH-GND | CRYSTAL_2.5X2 | X1 |  |  | 16MHz TCXO Clipped Sine Wave Oscillator 1.8V 4-SMD, No Lead | 1664-1323-1-ND |  |  |  |  |  |  |  | Taitien |  | TYKTBLSANF-16.000000
1 | 2.7k | R-US_0603-B-NOSILK | .0603-B-NOSILK | R21 | RESISTOR, American symbol |  | 2.7 kOhms ±1% 0.1W, 1/10W Chip Resistor 0603 (1608 Metric) Moisture Resistant Thick Film | CR0603-FX-2701ELFCT-ND |  |  |  |  |  |  |  | Bourns Inc. |  | CR0603-FX-2701ELF
1 | 22k | R-US_0603-B-NOSILK | .0603-B-NOSILK | R46 | RESISTOR, American symbol |  | 22 kOhms ±1% 0.1W, 1/10W Chip Resistor 0603 (1608 Metric) Automotive AEC-Q200 Thick Film | P22.0KHCT-ND |  |  |  |  |  |  |  | Panasonic Electronic Components |  | ERJ-3EKF2202V
1 | 22k | R-US_0603-C-NOSILK | .0603-C-NOSILK | R58 | RESISTOR, American symbol |  | 22 kOhms ±1% 0.1W, 1/10W Chip Resistor 0603 (1608 Metric) Automotive AEC-Q200 Thick Film | P22.0KHCT-ND |  |  |  |  |  |  |  | Panasonic Electronic Components |  | ERJ-3EKF2202V
1 | 22p | C-EU0402-B-NOSILK | .0402-B-NOSILK | C30 | CAPACITOR, European symbol |  | 22pF ±5% 50V Ceramic Capacitor C0G, NP0 0402 (1005 Metric) | 1276-1116-1-ND |  |  |  |  |  |  |  | Samsung Electro-Mechanics |  | CL05C220JB5NNNC
1 | 23.7k | R0603-23.7K-OHMS | .0603-C-NOSILK-RESISTOR | R36 | 23.7 kOhms ±1% 0.1W, 1/10W Chip Resistor 0603 (1608 Metric) Moisture Resistant Thick Film |  | 23.7 kOhms ±1% 0.1W, 1/10W Chip Resistor 0603 (1608 Metric) Moisture Resistant Thick Film | CR0603-FX-2372ELF-ND |  |  |  |  |  |  |  | Bourns |  | CR0603-FX-2372ELF
1 | 31.6k | R0603-31.6K-OHMS | .0603-C-NOSILK-RESISTOR | R5 | 31.6 kOhms ±1% 0.1W, 1/10W Chip Resistor 0603 (1608 Metric) Moisture Resistant Thick Film |  | 31.6 kOhms ±1% 0.1W, 1/10W Chip Resistor 0603 (1608 Metric) Moisture Resistant Thick Film | CR0603-FX-3162ELFCT-ND |  |  |  |  |  |  |  | Bourns |  | CR0603-FX-3162ELF
1 | 3p | C-EU0402-B-NOSILK | .0402-B-NOSILK | C31 | CAPACITOR, European symbol |  | 3pF ±0.25pF 50V Ceramic Capacitor C0G, NP0 0402 (1005 Metric) | 1276-1598-1-ND |  |  |  |  |  |  |  | Samsung Electro-Mechanics |  | CL05C030CB5NNNC |  |  |  |  |  |  |  |  |  |  |  | 50V
1 | 45.3k | R-US_0603-C-NOSILK | .0603-C-NOSILK | R48 | RESISTOR, American symbol |  | 45.3 kOhms ±1% 0.1W, 1/10W Chip Resistor 0603 (1608 Metric) Automotive AEC-Q200 Thick Film | RMCF0603FT45K3CT-ND |  |  |  |  |  |  |  | Stackpole Electronics Inc |  | RMCF0603FT45K3
1 | 47u | CAP0603-47UF | .0603-B-NOSILK-CAP | C120 | 47µF ±20% 6.3V Ceramic Capacitor X5R 0603 (1608 Metric) |  | 47µF ±20% 6.3V Ceramic Capacitor X5R 0603 (1608 Metric) | 478-11180-2-ND |  |  |  |  |  |  |  | AVX Corporation |  | 06036D476MAT2A |  |  |  |  |  |  |  |  |  |  |  | 6.3V
1 | 560p | C-EU0402-B-NOSILK | .0402-B-NOSILK | C38 | CAPACITOR, European symbol |  | 560pF ±5% 50V Ceramic Capacitor C0G, NP0 0402 (1005 Metric) | 1276-1709-1-ND |  |  |  |  |  |  |  | Samsung Electro-Mechanics |  | CL05C561JB5NNNC |  |  |  |  |  |  |  |  |  |  |  | 50V
1 | 560p | C-EU0402-B-NOSILK | .0402-B-NOSILK | C106 | CAPACITOR, European symbol |  | C - 0402, 560p, C0G, 50V | 1276-1709-1-ND |  |  |  |  |  |  |  | Samsung Electro-Mechanics |  | CL05C561JB5NNNC |  |  |  |  |  |  |  |  |  |  |  | 50V
1 | B8666 | B8666 | 1.7X1.3 | U18 | GPS SAW Extractor |  | 2.15GHz Frequency GPS RF SAW Filter (Sound Acoustic Wave) 1.5dB 46.84MHz Bandwidth 10-SMD, No Lead | B39162B8666L210CT-ND |  |  |  |  |  |  |  |  | Qualcomm (RF360 - A Qualcomm & TDK Joint Venture) | B39162B8666L210
1 | BFPXXXF | BFPXXXF | TSFP4 | Q7 | Infineon NPN RF Bipolar Transistor Family |  | RF Transistor NPN 4.7V 30mA 42GHz 160mW Surface Mount 4-TSFP | BFP740FH6327XTSA1CT-ND |  |  | Digikey |  |  |  |  |  | Infineon Technologies | BFP740FH6327XTSA1
1 | BFPXXXF | BFPXXXF | TSFP4 | Q9 | Infineon NPN RF Bipolar Transistor Family |  | RF Transistor NPN 4.7V 30mA 42GHz 160mW Surface Mount 4-TSFP | BFP740FH6327XTSA1CT-ND |  |  | Mouser |  |  |  |  | Infineon Technologies |  | BFP740FH6327XTSA1
1 | BGB7XXL7ESD | BGB7XXL7ESD | BGB7XXL7ESD | U20 | High Performance LNAs |  | LNA, general purpose | BGB741L7ESDE6327XTSA1CT-ND |  |  |  |  |  |  |  |  | Infineon Technologies | BGB741L7ESDE6327XTSA1‎
1 | GREEN | LED-GREEN0603 | LED-0603 | D3 | Green SMD LED |  | Green 573nm LED Indication - Discrete 2V 0603 (1608 Metric) | 732-12017-1-ND |  |  |  |  |  |  |  | Würth Elektronik |  | 150060VS55040 |  |  |  |  |  |  | DIO-00821 |  |  |  | GREEN
1 | J-SAMTEC-TFM-120-X1-XXX-D-RA | J-SAMTEC-TFM-120-X1-XXX-D-RA | J-SAMTEC-TFM-120-X1-XXX-D-RA | J6 |  |  | Connector Header Through Hole, Right Angle 40 position 0.050" (1.27mm) | SAM10145-ND |  |  |  |  |  |  |  | Samtec |  | TFM-120-01-L-D-RA
1 | MAC-24+ | MAC-24+ | MAC-24+ | U16 | RF Mixer, Diode Ring, 0.3 - 12 GHz |  | RF Mixer, Diode Ring, 0.3 - 12 GHz |  |  |  | Mini-Circuits |  |  |  |  |  | Mini-Circuits | MAC-24+
1 | MAX6374KA-T21-0078H-L | MAX6374KA-T21-0078H-L | 21-0078H-L | U32 |  |  |  | MAX6374KA+TCT-ND |  | Supervisor Push-Pull, Totem Pole 1 Channel SOT-23-8 |  |  |  |  |  | Maxim Integrated |  | max6374kat |  |  |  |  |  |  |  |  |  |  |  |  | Maxim Integrated Products
1 | MOSFET-P-N-PAIR | MOSFET-P-N-PAIR | SOT23-6 | Q6 |  |  | Mosfet Array N and P-Channel 20V 1.34A, 1.14A 1.12W Surface Mount SOT-26 | DMC2700UDM-7CT-ND |  |  |  |  |  |  |  | Diodes Incorporated |  | DMC2700UDM-7
1 | ORESAT-DEBUG-CONNECTOR-CARD | ORESAT-DEBUG-CONNECTOR-CARD | TE_2-1734592-0 | J5 |  |  | 20 Position FPC Connector Contacts, Bottom 0.020" (0.50mm) Surface Mount, Right Angle | A100287CT-ND |  |  |  |  |  |  |  | TE Connectivity AMP Connectors |  | 2-1734592-0
1 | PMOS | BSS84 | SOT23 | Q10 | P-CHANNEL MOS FET |  | P-Channel 50V 130mA (Ta) 360mW (Ta) Surface Mount SOT-23-3 | BSS84CT-ND |  |  |  |  |  |  |  | ON Semiconductor |  | BSS84 |  |  |  |  |  | 8
1 | SN65220 | SN65220 | SOT23-6 | D11 |  |  | ESD Suppressors / TVS Diodes Sngl Port Transient Suppressor |  |  |  |  |  |  |  |  | Texas Instruments |  | SN65220DBVRG4 |  | 595-SN65220DBVRG4
1 | TAITIEN-TY | TAITIEN-TY | 2.5X2.0 | X4 | Clipped Sine Wave TCXO |  | 16MHz TCXO Clipped Sine Wave Oscillator 1.8V 4-SMD, No Lead | 1664-1323-1-ND |  |  |  |  |  |  |  | Taitien |  | TYKTBLSANF-16.000000 |  |  |  |  |  |  |  |  |  | X
1 | TAITIEN-TY | TAITIEN-TY | 2.5X2.0 | X3 | Clipped Sine Wave TCXO |  | 16MHz TCXO Clipped Sine Wave Oscillator 1.8V 4-SMD, No Lead | 1664-1323-1-ND |  |  | Digikey |  |  |  |  |  | Taitien | TYKTBLSANF-16.000000
1 | TPS259620 | TPS2596XX | SO-POWERPAD-8 | U27 | TPS2596XX - eFuse With Accurate Current Monitor and Fast |  | Electronic Fuse Regulator 2A 8-SO PowerPad | 296-TPS259620DDATCT-ND |  |  |  |  |  |  |  | Texas Instruments |  | TPS259620DDAT
1 | TPS259621 | TPS2596XX | SO-POWERPAD-8 | U4 | TPS2596XX - eFuse With Accurate Current Monitor and Fast |  | Electronic Fuse Regulator 2A 8-SO PowerPad | 296-TPS259621DDATCT-ND |  |  |  |  |  |  |  | Texas Instruments |  | TPS259621DDAT
1 | TPS62111RSA | TPS6211X | S-PVQFN-16 | U5 | TPS6211x 17-V, 1.5-A, Synchronous Step-Down Converter |  | Buck Switching Regulator IC Positive Fixed 3.3V 1 Output 1.5A 16-VQFN Exposed Pad | 296-20670-1-ND |  |  |  |  |  |  |  | Texas Instruments |  | TPS62111RSAT
1 | TPS62112 | TPS6211X | S-PVQFN-16 | U26 | TPS6211x 17-V, 1.5-A, Synchronous Step-Down Converter |  | Buck Switching Regulator IC Positive Fixed 5V 1 Output 1.5A 16-VQFN Exposed Pad | 296-19717-1-ND |  |  |  |  |  |  |  | Texas Instruments |  | TPS62112RSAT
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

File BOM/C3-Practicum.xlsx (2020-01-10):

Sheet: C3-Board
Bill Of Materials
Source: bpf-L-band-BP0805.sch | oresat-c3-prototype |  | P/DNP = | Place/Do Not Place (DNP is for final production boards)
Modified: 2019-11-25 |  |  | Generic = | Any generic part with the same characteristics are OK (e.g., bypass cap)
Revision: 1
Cnt | Status | Part References | P/DNP | Mfg | Mfg PN | Description | Distributor | Dist. PN | Generic | Notes | URL
5 |  | C1,4,5,10,20 | P | Yageo | CC0603JRX7R6BB105 | 1uF Ceramic Cap, 0603, 5%, 10V | Digikey | 311-3484-2-ND | Y
9 |  | C2,3,6,8,9,13,15,17,22 | P | Yageo | CC0402JRX7R6BB104 | 0.1uF Ceramic Cap, 0402, 5%, 10V | Digikey | 311-3757-2-ND | Y
1 |  | C7 | P | Samsung | CL21X106KPYNNNE | 10uF ceramic cap, 0805, 10%, 10V | Digikey | 1276-3025-2-ND | Y
1 |  | C12 | P | Murata | GRM21BC81A226ME44L | 22uF ceramic cap, 0805, 20%, 10V | Digikey | 490-14657-2-ND | Y
2 |  | C11, C16 | P | Yageo | CC0402JRNPO9BN200 | 20pF ceramic cap, 0402, 20%, 6.3V | Digikey | 311-1417-1-ND | Y
1 |  | C14 | P | Murata | GRM188C81C225KA12D | 2.2uF ceramic cap, 0603, 10%, 16V | Digikey | 490-11993-1-ND | Y
1 |  | C18 | P | Taiyo Yuden | LMK316BC6476ML-T | 47uF ceramic cap, 1206, 20%, 10 | Digikey | 587-6459-1-ND | Y
3 |  | D1,D2,D5 | P | SunLED | XZVG68W-2 | Green LED, 0402, 2.1Vf, 20mA | Digikey | 1497-1219-1-ND | Y
1 |  | D3 | P | Inolux | IN-S42BTR | Red LED, 0402, 2.1Vf, 20mA | Digikey | 1830-IN-S42BCT-ND | Y
1 |  | D4 | P | Inolux | IN-S42BT5A | Amber LED, 0402, 2Vf, 5mA | Digikey | 1830-IN-S42BT5ACT-ND | Y
1 |  | D7 | P | Diodes Incorporated | 1N4148WS-7-F | 1N4148 Diode, SOD-323, 1.25 Vf, 150mA | Digikey | 1N4148WS-FDICT-ND | Y
1 |  | J6 | P | Samtec Inc. | TFM-120-01-H-D-RA | Connector Header Through Hole, Right Angle 40 position 0.050" (1.27mm) | Digikey | TFM-120-01-H-D-RA-ND | N
2 |  | J7 | P | Samtec Inc. | FTSH-105-01-F-DV-K | SMT Microheader, 2x5, 0.050" (1.27mm), unshrouded | Digikey | SAM8796-ND | Y
1 |  | J8 | P | 4UCON Technology Inc | ??? | SD/MMC card Socket | Sparkfun | PRT-12769 | N
4 |  | J9,10,11,12 | P | Harwin Inc. | M50-3500842 | Connector Header Through Hole 16 position 0.050" (1.27mm) | Digikey | 952-1385-ND | N
1 |  | L2 | P | ECS Inc. | ECS-MPI4040R4-6R8-R | 6.8uH Inductor, SMD, 20%, 2.4A, 3.2A sat | Digikey | XC2337CT-ND | N
4 |  | R1,2,3,4 | P | Panasonic | ERJ-2RKF2701X | 2.7k Resistor, 0402, 1%, 0.1W | Digikey | P2.70KLCT-ND | Y
1 |  | R5 | P | Panasonic | ERJ-2RKF3162X | 31.6k Resistor, 0402, 1%, 0.1W | Digikey | P31.6KLCT-ND | Y
1 |  | R6 | P | Panasonic | ERJ-2RKF3091X | 3.09k Resistor, 0402, 1%, 0.1W | Digikey | P3.09KLCT-ND | Y
8 |  | R7,9,16,17,18,20,24,27 | P | Panasonic | ERJ-2RKF1002X | 10k Resistor, 0402, 1%, 0.1W | Digikey | P10.0KLCT-ND | Y
3 |  | R8,11,13 | P | Panasonic | ERJ-2RKF4701X | 4.7k Resistor, 0402, 1%, 0.1W | Digikey | P4.70KLCT-ND | Y
2 |  | R10,12 | P | Panasonic | ERJ-3GEY0R00V | 0 ohm Resistor, 0603, 1%, 0.1W | Digikey | P0.0GCT-ND | Y
1 |  | R19 | P | Panasonic | ERJ-2RKF10R0X | 10 Resistor, 0402, 1%, 0.1W | Digikey | P10.0LCT-ND | Y
1 |  | R36 | P | Panasonic | ERJ-2RKF2372X | 23.7k Resistor, 0402, 1%, 0.1W | Digikey | P23.7KLDKR-ND | Y
1 |  | Q1 | P | STMicroelectronics | STT4P3LLH6 | P-Channel, SMD SOT-23-6, 30V 4A (Ta) 1.6W (Ta) | Digikey | 497-15521-1-ND | Y
1 |  | U1 | P | Maxim Integrated | MAX892LEUA+T | Power Switch/Driver 1:1 P-Channel 250mA 8-uMAX | Mouser | 700-MAX892LEUAT | N
2 |  | U2,U3 | P | Texas Instruments | TCAN330DCNR | 1/1 Transceiver CANbus SOT-23-8 | Digikey | 296-46215-1-ND | N
1 |  | U4 | P | Texas Instruments | TPS259621DDAT | Electronic Fuse Regulator 2A 8-SO PowerPad | Digikey | 296-TPS259621DDATCT-ND | N
1 |  | U5 | P | Texas Instruments | TPS62111RSAR | Buck Switching Regulator IC Positive Fixed 3.3V 1 Output 1.5A 16-VQFN Exposed Pad | Digikey | 296-37681-1-ND | N
1 |  | U6 | P | Maxim Integrated | MAX6373KA+T | Supervisor Open Drain or Open Collector 1 Channel SOT-23-8 | Digikey | MAX6373KA+TCT-ND | N
1 |  | U7 | P | STMicroelectronics | STM32F446RET6 | ARM® Cortex®-M4 STM32F4 Microcontroller IC 32-Bit 180MHz 512KB (512K x 8) FLASH 64-LQFP (10x10) | Digikey | 497-15376-ND | N
1 |  | X1 | P | ECS Inc. | ECS-160-10-36Q-ES-TR | 16MHz ±30ppm Crystal 10pF 80 Ohms 4-SMD, No Lead | Digikey | XC2181CT-ND | N
Revision History
Rev | Date | Notes
1 | 2019-11-22 | Initial BOM.
 | x | Assembled 1x board
 | x | Assembled 1x board

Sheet: template
Bill Of Materials
Source: schematic-name.sch |  |  | P/DNP = | Place/Do Not Place (DNP is for final production boards)
Modified: yyyy-mm-dd |  |  | Generic = | Any generic part with the same characteristics are OK (e.g., bypass cap)
Revision: 1
Cnt | Status | Part References | P/DNP | Mfg | Mfg PN | Description | Distributor | Dist. PN | Generic | Notes | URL
Revision History
Rev | Date | Notes
1 | yyyy-mm-dd | Initial BOM.

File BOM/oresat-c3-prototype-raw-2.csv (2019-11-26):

Part | Value | Device | Package | Description | DIS | DPN | MANUFACTURER_PART_NUMBER | MFR | MPN | PROD_ID | SF_ID | VALUE | VENDOR
C1 | 1u | C-EU0603-B-NOSILK | .0603-B-NOSILK | CAPACITOR, European symbol | Digi-Key | 1276-1001-1-ND |  | Samsung | CL05B104KO5NNNC
C2 | 100n | C-EU0402-B-NOSILK | .0402-B-NOSILK | CAPACITOR, European symbol | Digi-Key | 1276-1001-1-ND |  | Samsung | CL05B104KO5NNNC
C3 | 100n | C-EU0402-B-NOSILK | .0402-B-NOSILK | CAPACITOR, European symbol | Digi-Key | 1276-1001-1-ND |  | Samsung | CL05B104KO5NNNC
C4 | 1u | C-EU0603-B-NOSILK | .0603-B-NOSILK | CAPACITOR, European symbol | Digi-Key | 1276-1001-1-ND |  | Samsung | CL05B104KO5NNNC
C5 | 1u | C-EU0603-B-NOSILK | .0603-B-NOSILK | CAPACITOR, European symbol | Digi-Key | 1276-1001-1-ND |  | Samsung | CL05B104KO5NNNC
C6 | 100n | C-EU0402-B-NOSILK | .0402-B-NOSILK | CAPACITOR, European symbol | Digi-Key | 1276-1001-1-ND |  | Samsung | CL05B104KO5NNNC
C7 | 10u | C-EU0805-B-NOSILK | .0805-B-NOSILK | CAPACITOR, European symbol
C8 | 100n | C-EU0402-B-NOSILK | .0402-B-NOSILK | CAPACITOR, European symbol | Digi-Key | 1276-1001-1-ND |  | Samsung | CL05B104KO5NNNC
C9 | 100n | C-EU0402-B-NOSILK | .0402-B-NOSILK | CAPACITOR, European symbol | Digi-Key | 1276-1001-1-ND |  | Samsung | CL05B104KO5NNNC
C10 | 1u | C-EU0603-B-NOSILK | .0603-B-NOSILK | CAPACITOR, European symbol | Digi-Key | 1276-1001-1-ND |  | Samsung | CL05B104KO5NNNC
C11 | 20p | C-EU0402-B-NOSILK | .0402-B-NOSILK | CAPACITOR, European symbol | Digi-Key | 1276-6601-1-ND |  | Samsung | CL05C200JB51PNC
C12 | 22u | C-EU0805-B-NOSILK | .0805-B-NOSILK | CAPACITOR, European symbol
C13 | 100n | C-EU0402-B-NOSILK | .0402-B-NOSILK | CAPACITOR, European symbol | Digi-Key | 1276-1001-1-ND |  | Samsung | CL05B104KO5NNNC
C14 | 2.2u | C-EU0603-B-NOSILK | .0603-B-NOSILK | CAPACITOR, European symbol | Digi-Key | 1276-1001-1-ND |  | Samsung | CL05B104KO5NNNC
C15 | 100n | C-EU0402-B-NOSILK | .0402-B-NOSILK | CAPACITOR, European symbol | Digi-Key | 1276-6601-1-ND |  | Samsung | CL05C200JB51PNC
C16 | 20p | C-EU0402-B-NOSILK | .0402-B-NOSILK | CAPACITOR, European symbol | Digi-Key | 1276-6601-1-ND |  | Samsung | CL05C200JB51PNC
C17 | 100n | C-EU0402-B-NOSILK | .0402-B-NOSILK | CAPACITOR, European symbol | Digi-Key | 1276-1001-1-ND |  | Samsung | CL05B104KO5NNNC
C18 | 47u | C-EU1206-B | 1206-B | CAPACITOR, European symbol | Digi-Key | 1276-6601-1-ND |  | Samsung | CL05C200JB51PNC
C20 | 1u | C-EU0603-B-NOSILK | .0603-B-NOSILK | CAPACITOR, European symbol | Digi-Key | 1276-1001-1-ND |  | Samsung | CL05B104KO5NNNC
C22 | 100n | C-EU0402-B-NOSILK | .0402-B-NOSILK | CAPACITOR, European symbol | Digi-Key | 1276-1001-1-ND |  | Samsung | CL05B104KO5NNNC
D1 | GREEN | LED-GREEN0603 | LED-0603 | Green SMD LED |  |  |  |  |  |  |  | GREEN
D2 | GREEN | LED-GREEN0603 | LED-0603 | Green SMD LED |  |  |  |  |  |  |  | GREEN
D3 | RED | LED-GREEN0603 | LED-0603 | Green SMD LED |  |  |  |  |  | DIO-00821 |  | GREEN
D4 | AMBER | LED-GREEN0603 | LED-0603 | Green SMD LED |  |  |  |  |  |  |  | GREEN
D5 | GREEN | LED-GREEN0603 | LED-0603 | Green SMD LED |  |  |  |  |  |  |  | GREEN
D7 | 1N4148 | DIODESOD | SOD-323 | Diode
J6 | J-SAMTEC-TFM-120-X1-XXX-D-RA | J-SAMTEC-TFM-120-X1-XXX-D-RA | J-SAMTEC-TFM-120-X1-XXX-D-RA |  |  |  |  | Samtec | TFM-120-01-L-D-RA
J7 | FTSH-105-XX-X-DV-K | FTSH-105-XX-X-DV-K | CON10_2X5_DUK_FTSH |  |  |  |  | Samtec | FTSH-105-01-F-DV-K
J8 | SD_CARD_SOCKET | SD_CARD_SOCKET | SD | SD Memory Card Connector (standard "large" size) |  |  |  |  |  | CONN-11976 | PRT-12769
J9 | 2X8X1.27 | 2X8X1.27 | 2X8X1.27
J10 | 2X8X1.27 | 2X8X1.27 | 2X8X1.27
J11 | 2X8X1.27 | 2X8X1.27 | 2X8X1.27
J12 | 2X8X1.27 | 2X8X1.27 | 2X8X1.27
L2 | 6.8u | L-ECS-MPI4040 | ECS-MPI4040 |  |  |  |  | ECS | ECS-MPI4040R4-6R8-R
Q1 | MOSFET-PCH-SOT23-6 | MOSFET-PCH-SOT23-6 | SOT23-6 | P channel MOSFET in an SOT23-6
R1 | 2.7k | R-US_0402-B-NOSILK | .0402-B-NOSILK | RESISTOR, American symbol | Digi-Key | 1276-4275-1-ND |  | Samsung | RC1005F6653CS
R2 | 2.7k | R-US_0402-B-NOSILK | .0402-B-NOSILK | RESISTOR, American symbol | Digi-Key | 1276-4275-1-ND |  | Samsung | RC1005F6653CS
R3 | 2.7k | R-US_0402-B-NOSILK | .0402-B-NOSILK | RESISTOR, American symbol | Digi-Key | 1276-4275-1-ND |  | Samsung | RC1005F6653CS
R4 | 2.7k | R-US_0402-B-NOSILK | .0402-B-NOSILK | RESISTOR, American symbol | Digi-Key | 1276-4275-1-ND |  | Samsung | RC1005F6653CS
R5 | 31.7k | R-US_0402-B-NOSILK | .0402-B-NOSILK | RESISTOR, American symbol | Digi-Key | 1276-4275-1-ND |  | Samsung | RC1005F6653CS
R6 | 3.1k | R-US_0402-B-NOSILK | .0402-B-NOSILK | RESISTOR, American symbol | Digi-Key | 1276-4275-1-ND |  | Samsung | RC1005F6653CS
R7 | 10k | R-US_0402-B-NOSILK | .0402-B-NOSILK | RESISTOR, American symbol | Digi-Key | 1276-4275-1-ND |  | Samsung | RC1005F6653CS
R8 | 4.7k | R-US_0402-B-NOSILK | .0402-B-NOSILK | RESISTOR, American symbol
R9 | 10k | R-US_0402-B-NOSILK | .0402-B-NOSILK | RESISTOR, American symbol | Digi-Key | 1276-4275-1-ND |  | Samsung | RC1005F6653CS
R10 | NP | R-US_0402-B-NOSILK | .0402-B-NOSILK | RESISTOR, American symbol | Digi-Key | 1276-4275-1-ND |  | Samsung | RC1005F6653CS
R11 | 4.7k | R-US_0402-B-NOSILK | .0402-B-NOSILK | RESISTOR, American symbol
R12 | 0 | R-US_0603-B-NOSILK | .0603-B-NOSILK | RESISTOR, American symbol | Digi-Key | 1276-4275-1-ND |  | Samsung | RC1005F6653CS
R13ERJ-2RKF2372X | 4.7k | R-US_0402-B-NOSILK | .0402-B-NOSILK | RESISTOR, American symbol
R16 | 10k | R-US_0402-B-NOSILK | .0402-B-NOSILK | RESISTOR, American symbol | Digi-Key | 1276-4275-1-ND |  | Samsung | RC1005F6653CS
R17 | 10k | R-US_0402-B-NOSILK | .0402-B-NOSILK | RESISTOR, American symbol | Digi-Key | 1276-4275-1-ND |  | Samsung | RC1005F6653CS
R18 | 10k | R-US_0402-B-NOSILK | .0402-B-NOSILK | RESISTOR, American symbol
R19 | 10 | R-US_0402-B-NOSILK | .0402-B-NOSILK | RESISTOR, American symbol
R20 | 10k | R-US_0402-B-NOSILK | .0402-B-NOSILK | RESISTOR, American symbol
R24 | 10k | R-US_0402-B-NOSILK | .0402-B-NOSILK | RESISTOR, American symbol
R27 | 10k | R-US_0402-B-NOSILK | .0402-B-NOSILK | RESISTOR, American symbol | Digi-Key | 1276-4275-1-ND |  | Samsung | RC1005F6653CS
R36 | 23.9k | R-US_0402-B-NOSILK | .0402-B-NOSILK | RESISTOR, American symbol | Digi-Key | 1276-4275-1-ND |  | Samsung | RC1005F6653CS
U$1 | ORESAT-CARD-V1.1-3XRF | ORESAT-CARD-V1.1-3XRF | ORESAT-CARD-V1.1-3XRF
U1 | MAX892LEUA+T21-0036K-L | MAX892LEUA+T21-0036K-L | 21-0036K-L | MAX891L / MAX892L |  |  | MAX892LEUA+T |  |  |  |  |  | Maxim Integrated Products
U2 | TCAN330 | TCAN330 | SOT23-8_TI-DCN |  |  |  |  | Texas Instruments | TCAN330GDCNT
U3 | TCAN330 | TCAN330 | SOT23-8_TI-DCN |  |  |  |  | Texas Instruments | TCAN330GDCNT
U4 | TPS259621 - eFuse | TPS2596XX | SO-POWERPAD-8 | TPS2596XX - eFuse With Accurate Current Monitor and Fast
U5 | TPS62111RSA | TPS6211X | S-PVQFN-16 | TPS6211x 17-V, 1.5-A, Synchronous Step-Down Converter |  |  |  | TI | TPS62111RSA
U6 | MAX6374KA-T21-0078H-L | MAX6374KA-T21-0078H-L | 21-0078H-L |  |  |  | max6374kat |  |  |  |  |  | Maxim Integrated Products
U7 | STM32F446RE | STM32F446RE | QFP-10X10-64
X1 | 16MHZ-2.5x2mm | CRYSTAL-WITH-GND | CRYSTAL_2.5X2 |  | Digi-Key | XC2181CT-ND |  | ECS Inc. | ECS-160-10-36Q-ES-TR

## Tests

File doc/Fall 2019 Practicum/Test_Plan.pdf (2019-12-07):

# Homework 8 Test Plan

Revision 1.1

## Practicum Team 7

## Miles Simpson, Robin Ekeya, Kirk Jungles, Mikhail Mayers

12/6/2019

# Department of Electrical and

# Computer Engineering

# Portland State University

# Table of Contents

Table of Contents | 1
Introduction | 2
Reference Documents | 2
ORESAT C3 Overview | 3
Objectives | 4
Pretest Preparation | 5
Required Equipment | 5
Unit Tests | 5
Power Input/Output | 5
Microcontroller | 5
Watchdog Timer | 5
Radio TX | 5
Radio RX | 5
OPD Interface | 5
MMC | 5
Integration Tests | 6
Microcontroller | 6
Watchdog Timer | 6
OPD | 6
CAN Transceivers | 6
Radios | 6
MMC | 6
Acceptance Tests | 6
Power | 6
OPD | 6
CAN | 6
Watchdog shutdown signal | 6
Radios | 6
MMC | 6
Physical Form Factor | 7
Test Cases | 7

# 1. Introduction

This document will serve as a description of our test plan for our practicum project, ORESAT Communication Command and Control(C3) Board. Our ultimate objective is to determine whether or not our device fulfills its requirements and will be accepted by our customer, OreSat.
We will provide an overview of the OreSat C3 project, reference documents for our design process, pretest preparation measures, system test procedures and expected outcomes for each module of our project, integration testing procedures and expected outcomes, and acceptance testing procedures that will determine if our device fulfills its “must”-specified requirements as outlined in our initial product design specifications.
Because all modules are effectively integrated into a single printed circuit board, it would be highly impractical to test each module as a stand-alone block in a separate circuit without already being connected to other elements of the system. The layout of the board was designed with this in mind and includes test points. Accordingly, our build and test procedure will be roughly as follows:
1. Stuff and solder entire board with all components and test points
2. Provide current limited power source and check that power level is within expected range for all modules
3. Provide full normal operation power and test performance of each module individually
4. Test the interfaces and interactions between the various modules
5. Test that the entire system performs in accordance with the requirements

# 2. Reference Documents

2.1. Our GitHub repository has served as the central hub for all of our design work and documentation, and is available here: https://github.com/oresat/oresat-c3
2.2. Our Product Design Specifications document details the expected performance of the device and will be the metric with which the acceptability of our product is measured. This will serve as a useful reference for acceptance testing: https://github.com/oresat/oresat-c3/blob/master/doc/OreSat_C3_PDS.pdf
2.3. The CAN protocol is based on an extension of the CANopen specification known as ECSS-E-ST-50-15C – CANbus extension protocol (1 May 2015) (https://ecss.nl/standard/ecss-e-st-50-15c-space-engineering-canbus-extension-protocol-1-may-2015/)

2.4. OPD Endpoints are controlled via the MAX7310 (https://datasheets.maximintegrated.com/en/ds/MAX7310.pdf) in order to activate cards and get circuit breaker status
2.5. The OreSat CLSI Application (http://oresat.org/mission/oresat-2016-csli-application-r6-PUBLIC.pdf) describes the overall OreSat design, purpose, and functionality for which we are building the C3 component
2.6. Our System Functional Decomposition document details the expected performance of each subsystem and shows how the subsystems relate to one another. This will serve as a useful reference for both Systems and Integration Testing:
2.7. https://github.com/oresat/oresat-c3/blob/master/doc/System_Design-Functional_Decomposition.pdf (https://github.com/oresat/oresat-c3/blob/master/doc/System_Design-Functional_Decomposition.pdf)

# 3. ORESAT C3 Overview

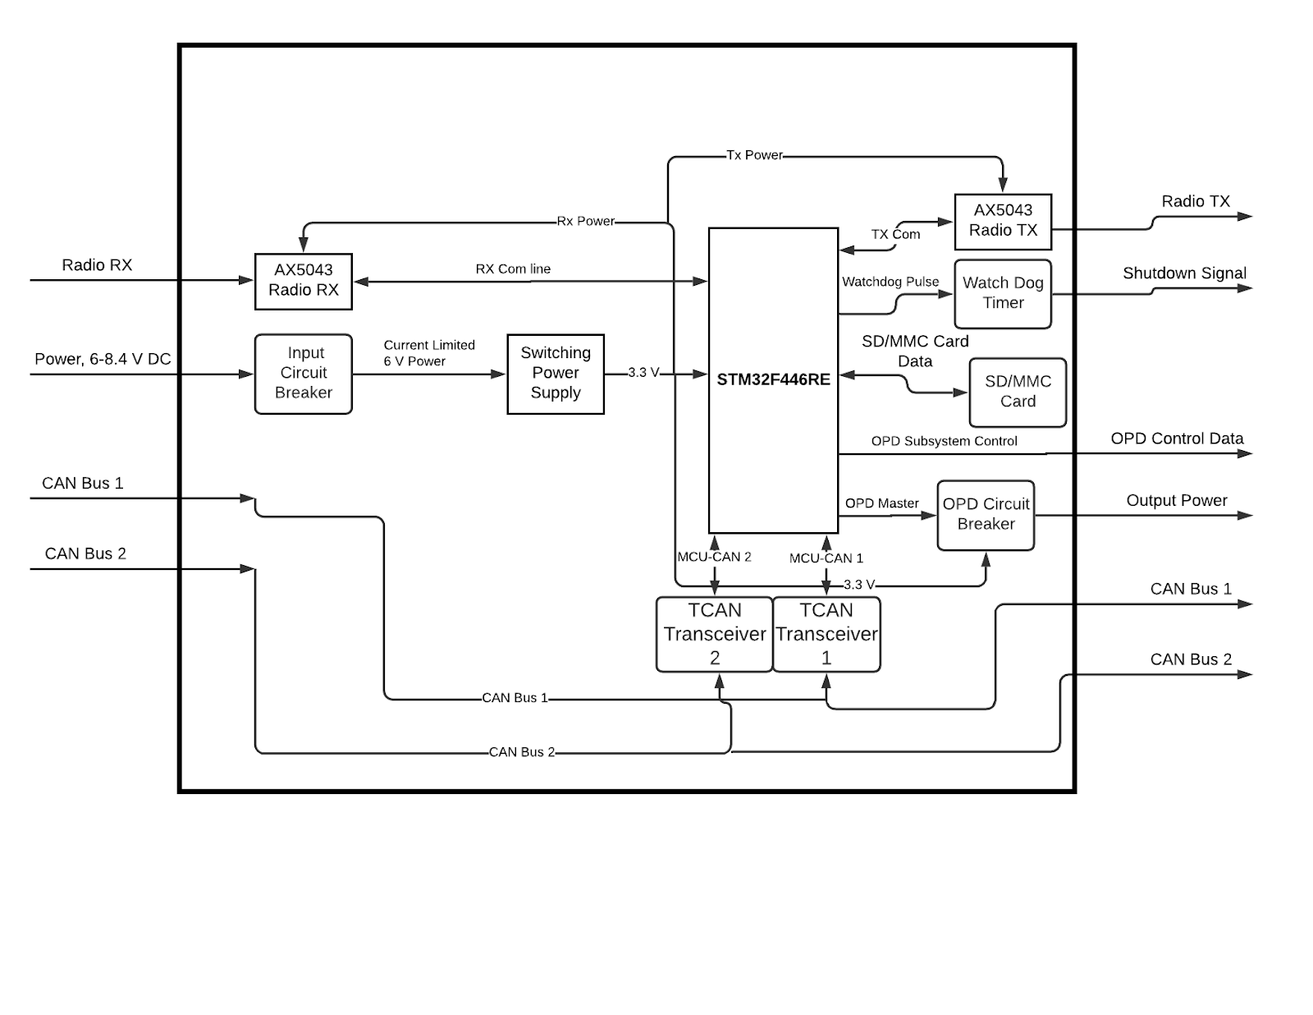
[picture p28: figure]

Figure 1: OreSat C3 Block Diagram OreSat is an open-source cubesat project that is currently developing Oregon’s first satellite to be launched into space. Our product is the command, control and communications (C3) module for OreSat’s cubesat. It integrates several different sensors and actuators involved in the top level control of the OreSat project. It is responsible for controlling the power and data flow to and from various subsystems within the satellite.
It receives a 6-8.4 V Power supply from an external solar cell module, which is fed into an Input Circuit Breaker module that provides overcurrent and undervoltage protection. This is then fed to a Switching Power Supply module which steps the voltage down to a regulated 3.3 V bus that is used to power an STM32 Microcontroller Unit(MCU) and is fed to the Oresat Power Domain(OPD) Circuit Breaker module, which receives control signals from the MCU and provides power to all external subsystems, and directly to the Rx and Tx Radio modules. C3 will also expect to receive radio transmissions from an external source on the Radio Rx line, which is then fed directly to the MCU through an SPI interface. The system will also receive data from external modules on the CAN Bus 1 and CAN Bus 2 lines, which are fed to TCAN Transceivers 1 and 2, and then sent to the MCU through MCU-CAN 1 and 2.
The MCU unit will also send SPI data to the Radio Tx module through the Tx Com line, which will then be sent to an external module for propagation.The MCU will also send a pulse to the Watchdog Timer, which will, in the absence of a pulse from the MCU, send a data packet down the Shutdown Signal line to an external module that will cut off power to the entire system. The MCU will also be storing data onto an MMC card, which will serve as memory storage. The MCU will also control power to the entire satellite through the OPD system by sending control signals to each external module through the OPD Control Data line, which controls power locally at each external module, and by sending signals on the OPD Master line which controls the OPD Circuit Breaker module, which provides power to all external modules in the satellite. Command and control data will also be sent from the MCU to the TCAN Transceiver 1 and 2 modules, which will then send data to external modules down the CAN Bus 1 and 2 lines. The minimum requirements for our product is that it must:
1. Conform to OreSat card cage specifications
2. Be able to be powered from OreSat power bus
3. Be able to provide power to OreSat Power Domain
4. Be capable of interfacing with OreSat Power Domain
5. Be capable of interfacing with OreSat critical subsystems
6. Be able to reset in case of radiation induced single event latch-up of the C3 card
7. Provide communications interface with radio modules
8. Provide non-volatile data storage

# 4. Objectives

In order to ensure our project meets specifications, we must perform a series of tests to gradually bring up and verify components of the card, and incrementally integrate components together. The objectives of the tests are as follows
- Unit Tests: This stage of testing verifies individual subsystems of our card, such as power, work as expected. Most of this unit is applying power, testing voltages, pulling high or low different input test points, and verifying expected changes in outputs of blocks. It is done tested in discrete units.

- Integration test: This stage tests the interface between various subsystems. It verifies that subsystems can communicate correctly and that there are no unexpected conditions present in communication.
- Acceptance test: This stage tests that the entire board meets requirements previously established in our Product Design Specifications document.

# 5. Pretest Preparation

## 5.1. Required Equipment

5.1.1. Power supply capable of providing up to 8.4V and 400mA
5.1.2. Multimeter capable of measuring voltage and at least 100mA of current
5.1.3. Logic Analyzer capable of probing I2C and SPI communications
5.1.4. OreSat Protocard and FlatSat Bus to test interface with other subsystems

# 6. Unit Tests

## 6.1. Power Input/Output

6.1.1. Test the Input Circuit Breaker
6.1.2. Test the 3.3V Switching Power Supply
6.1.3. Test the OPD Circuit Breaker

## 6.2. Microcontroller

6.2.1. Test microcontroller is programmable with ST-LINK

## 6.3. Watchdog Timer

6.3.1. Test Watchdog Timer shutdown functionality

## 6.4. Radio TX

6.4.1. Verify power applied to TX radio and SPI lines

## 6.5. Radio RX

6.5.1. Verify power applied to RX radio and SPI lines

## 6.6. OPD Interface

6.6.1. Verify OPD I2C lines are pulled up correctly

## 6.7. MMC

6.7.1. Verify power control circuit for MMC card

# 7. Integration Tests

## 7.1. Microcontroller

7.1.1. Test debugging interface of microcontroller
7.1.2. Test serial interface of microcontroller

## 7.2. Watchdog Timer

7.2.1. Test ability to “kick” watchdog from MCU

## 7.3. OPD

7.3.1. Test power application to OPD circuit
7.3.2. Test I2C transaction with OPD circuit endpoint

## 7.4. CAN Transceivers

7.4.1. Test transmit and receive capability on CAN1 bus
7.4.2. Test transmit and receive capability on CAN2 bus

## 7.5. Radios

7.5.1. Test SPI communications with radios

## 7.6. MMC

7.6.1. Test SPI communications with MMC
7.6.2. Test ability to read and write data

# 8. Acceptance Tests

## 8.1. Power

8.1.1. Verify the voltage range of OreSat VBUS is sufficient to power the card and that circuit breakers perform as expected

## 8.2. OPD

8.2.1. Test that MCU can power and control OPD subsystem by issuing commands to circuit breakers on bus attached cards

## 8.3. CAN

8.3.1. Test that MCU can issue commands and receive telemetry from cards via the ECSS protocol on at least CAN1

## 8.4. Watchdog shutdown signal

8.4.1. Test that Watchdog timer will power cycle the board only if communication between it and the microcontroller ceases

## 8.5. Radios

8.5.1. Test communication between board and ground station

## 8.6. MMC

8.6.1. Test telemetry storage and retrieval from MMC card

## 8.7. Physical Form Factor

8.7.1. Verify card meets OreSat card specifications

# 9. Test Cases

Test Writer: Miles Simpson
Test Case Name: | Test Input Circuit Breaker | Test ID #: | 5.1.1
Description: | This test verifies proper functionality of the C3 card’s input power circuit breaker. It ensures power is supplied through it to VBUSP, and that it current limits properly during a short. | Type:
X | white box
| black box

Tester Information
Name of Tester: | | Date:
Hardware Ver: | 1.0 | Time:
Equipment: | Power Supply, Multimeter
Setup: | PS set to 7.5V, 50mA max initially
s t e p | Action | Expected Result | p a s s | f a i l | N/ A | Comments
1 | Apply power to VBUS and verify VBUS and VBUSP with multimeter (VBUS pin on JP10, and TP20 respectively) | 7.5V is measured at VBUS on JP10 and VBUSP at TP20, and current on power supply <50mA
2 | Increase supply current limit to 400mA and briefly short VBUSP at TP20 to ground with large gauge wire | Verifying that power supply reads ~302mA maximum current supplied to card during short
3 | Short VBUSP at TP20 to ground for extended period | Verify thermal cutoff occurs in TPS259621 within 2 seconds

4
5
6
Overall test result:

Test Writer: Miles Simpson
Test Case Name: | Test OPD Circuit Breaker | Test ID #: | 5.1.3
Description: | This test verifies proper functionality of the C3 card’s OPD output circuit breaker by testing the enable signal and current limiting functionality of the circuit. | Type:
X | white box
| black box

Tester Information
Name of Tester: | | Date:
Hardware Ver: | 1.0 | Time:
Equipment: | Power Supply, Multimeter
Setup: | PS set to 7.5V, 100mA max, connected to VBUS
s t e p | Action | Expected Result | p a s s | f a i l | N/ A | Comments
1 | Measure voltage of !OPD_ENABLE at TP13 using Multimeter | !OPD_ENABLE is pulled up to ~3.3V
2 | Ground TP13 | Verify LED D4 turns on
3 | While grounded, measure voltage of !FAULT at TP8 | !FAULT is high (~3.3V) and LED D5 is on
4 | Using 100mA multimeter current probe, short OPD_PWR to ground | Verify current does not exceed ~50mA

5
6
Overall test result:

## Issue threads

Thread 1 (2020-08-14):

Wrong footprint for X1

davidalay, 2020-08-14:
The footprint on the board for X1 is too small and should be changed to fit the standard 16 MHz crystal we use for Oresat

Closed 2020-12-13.

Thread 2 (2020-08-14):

Solder mask pulled back too far

davidalay, 2020-08-14:
The solder mask is pulled back too far from the RF traces and some pads.  At some points it exposes other traces that should be covered by the solder mask.  Not a massive problem but should be fixed for the flight board.

glennl, 2020-10-16:
We determined that the solder mask T_Stop dimension on all new transmission lines with the name _***_PA$***_ can be changed. Also **_TX_TO_** and **_TX_OUT_** The new values can be changed to 3x the layer thickness (h). We find h=0.17mm so, 3*0.17 = 0.51mm. Since this is the dimension on each side, the total T_Stop would be 2x that value, or 1.02 mm. Currently the T_Stop is set to 2.1 mm.

andrewgreenberg, 2020-12-14:
Decided to move RF net clearance to 0.75 mm which is ~ 4x the dielectric thickness. Better than minimum of 3 and worse than the 5 some people say.

andrewgreenberg, 2020-12-14:
The TSTOP on the RF traces is 1.6 wide, which protects the ground copper with  0.18 mm of coverage on both sides.

andrewgreenberg, 2020-12-29:
Done! And in a markdown file in the doc folder.

Closed 2020-12-29.

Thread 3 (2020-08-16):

Missing Pull UP on U4

davidalay, 2020-08-16:
The TPS259621 needs an external pull up on the !FLT pin

Closed 2020-12-13.

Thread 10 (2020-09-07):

Add redundant RTCs capable of independent power cycling and tolerant of !SD event

heliochronix, 2020-09-07:
We need two additional RTCs with capacitors to maintain their power in the event of a !SD event (global watchdog shutdown), but that are also capable of being independently power cycled by the MCU.

andrewgreenberg, 2021-01-02:
Yeah, you don't get two. But I'll give you one. With EEPROM, and SRAM. And with a Cap/Supercap backup, with ability to power cycle it. It's the Micro Crystal RV-3028 Go nuts!

Closed 2021-01-02.

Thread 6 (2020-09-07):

Cream layer on U20 and U10 too small

davidalay, 2020-09-07:
the slots on the cream layer for U20 and U10 are too small, it is difficult the paste through.  I would suggest making them a tiny bit bigger (a little change goes a long way).

andrewgreenberg, 2020-12-13:
Fixed U10 (synthesizer) - it had custom solder paste apertures that were just too small.

U20 is a differen't beast. It's _small_. Not sure what to do, putting this off until other ICs are there.

Closed 2020-12-13.

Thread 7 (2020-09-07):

Wrong Attrtibutes

davidalay, 2020-09-07:
R3, R5, R19, R22, R44, R80, R81 have attributes that point to an 0402 PN but have an 0603 package.  I suggest using a PN in an 0603 package but at least make sure that the package of the footprint and the package of the PN agree.

Closed 2021-02-01.

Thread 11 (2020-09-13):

3.3V and 5.0V SPS inductor do not clear the Y frame bosses

andrewgreenberg, 2020-09-13:
All components > 1.5 mm tall must be OUTSIDE of the boss exclusion zone depicted in the TDOC layer on the +/-Y sides (the left and right of the board).

andrewgreenberg, 2020-12-29:
Fixed! Moved 5V SPS to near UHF radio that needs it, and moved 3.3V inboard.

Closed 2020-12-29.

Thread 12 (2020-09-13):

Add "pullout hole" in lower right corner of PCB (+X+Y corner) - see protocard holes.

andrewgreenberg, 2020-09-13:

andrewgreenberg, 2020-12-29:
Fixed in new card outline.

Closed 2020-12-29.

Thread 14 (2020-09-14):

!SD latches

davidalay, 2020-09-14:
If an inhibit switch is actuated and power is cut from the system, the !SD from the watchdog will latch

andrewgreenberg, 2021-01-07:
Nope: this turns out to be a battery issue we think. The WDT seems to work just fine independently; it certainly does not falsely  trigger on power up.

Closed 2021-01-07.

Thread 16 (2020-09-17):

Radio IRQ lines need to be on different pad numbers

heliochronix, 2020-09-17:
The radio IRQ lines need to be on different pad number from other GPIO ports. This is due to restrictions in the STM32 EXTI architecture as shown in the following image. Currently they are on PA8 and PD8, but one of them must be on a pin other than the respective port's pin "8".
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

andrewgreenberg, 2021-01-02:
LBAND_IRQ is now on PD12 and UHF_IRQ is now on PD10. Let me know if that does NOT work ASAP, else close this issue.

heliochronix, 2021-01-03:
Works

Closed 2021-01-03.

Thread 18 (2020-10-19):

Move components on RADIO_ANALOG_1 and N$5 to other side of input filter

glennl, 2020-10-19:
The idea is to have the RC filter for an analog input close to the CPU. This would cause the filter components and two nets currently placed to require rework. Andrew may reasonably argue this is not worth the effort. :) Parts of this are now airwires and there are two connections, RADIO_ANALOG_1 and N$5.

andrewgreenberg, 2020-12-29:
No room at the inn; leaving analog filters next to the log amps.

Closed 2020-12-29.

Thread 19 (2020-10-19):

Resolve 5V_U airwire

glennl, 2020-10-19:
Currently the supply 5V_U at R99 and Q4 has not been routed, and is still an airwire.

andrewgreenberg, 2020-12-29:
Fixed.

Closed 2020-12-29.

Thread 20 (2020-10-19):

Unused gates of IC1 and IC3 need inputs terminated

glennl, 2020-10-19:
Two unused gates need to be placed onto the schematic ??either IC1 or IC3?? and their unused inputs need to be tied to ground.

andrewgreenberg, 2020-12-29:
IC1 and IC3 have been replaced, this is no longer a problem.

Closed 2020-12-29.

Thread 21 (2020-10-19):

Thermal of U30 needs to be confirmed to clearly go to the right edge of the PCB

glennl, 2020-10-19:

andrewgreenberg, 2020-12-29:
Does now on layer 2 and 16, with a note on the right saying to keep these open. I removed BSTOP betwen the bottom of the board and the card edge, we could add a bus bar here if we wanted to.

Closed 2020-12-29.

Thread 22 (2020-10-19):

5th order LPF between AX5043 SE output and PA needed

glennl, 2020-10-19:
The requirements document (block diagram) shows a 5th order LPF between the AX5043 SE output, and the input of the PA. This has not been added.

Glenn and Vigely should confirm it is really needed.

glennl, 2020-10-21:
After discussion with Vigely, it's determined it is needed. There are significant magnitude harmonic products coming off of the AX5043, and the PA design will likely amplify them. The filter choice is the one Vigely used in his thesis work. and can be found at:
**_oresat-c3-rf/eagle/lpf-5th-order.sch_**

NB: Since the signal is still considered "small signal" at this point before amplification, small 0402 lumped components can still be used.

There was also discussion about adding another 5th order LPF **after** the PA, but we decided to leave this out because, (1) the PA will not be running anywhere near its 1 dB compression point (low in its linear range), and (2) the component sizes will need to be bigger, and the board is already getting a bit full. After testing this C3 Rev-4 version, we will need to decide if the is a good decision.

andrewgreenberg, 2020-12-29:
Glenn, II need this designed. Can you do that?

glennl, 2021-01-03:
Working on this right now. Should be small 0402 components, and there is a bunch of space currently available on the board for this.

glennl, 2021-01-03:
Andrew, Thanks for placing the circuit. We can close this issue once I determine the lumped component values.

glennl, 2021-01-04:
The very same LPF is used for the UHF Tx between the AX5043 output and the PA input (436 MHz), and the L-Band's IF between the mixer output and the AX5043 input (452-462 MHz).

Checking the component values with a 5th order LC Chebychev LPF calculator, the values produce a filter of the following specs:
   **_Cutoff freq:  560 MHz
   Zo: 50 ohm
   Passband ripple: 1 dB_**

This has been confirmed with Vigely

Closed 2021-01-04.

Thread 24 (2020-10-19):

RT1 Thermister needs to be re-wired

glennl, 2020-10-19:
RT1 Thermister was incorrectly wired in the schematic. Andrew knows the correct orientation.

- Found 402 Thermister in Library

- Re-config R84

- Add 10k pullup

andrewgreenberg, 2020-12-29:
Fixed! Now pulled up to 3.3v and we should be able to read temperature to a few degrees C.

Closed 2020-12-29.

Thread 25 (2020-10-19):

RF Log amps optional LPFs

glennl, 2020-10-19:
Values for the log amp output LPS need to be chosen. Currently they are set to 0 or NP.

- U32, R96, C140

- U33, R97, C141

glennl, 2021-03-08:
Leave these as they are. No additional filtering has been identified.
See page 8 of datasheet for LT5534.
https://www.analog.com/media/en/technical-documentation/data-sheets/5534fc.pdf

Closed 2021-03-08.

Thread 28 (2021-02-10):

M4_PA_ENABLE and !M4_LNA_ENABLE need pull down / pull up respectively

andrewgreenberg, 2021-02-10:

andrewgreenberg, 2021-02-10:
* M4_PA_ENABLE (Needs pull down, default M4 output is low)
* !M4_LNA_ENABLE (needs pull up to 3.3V, default M4 output is high)
* M4_TOT_CLEAR (needs pull up to 3.3V?? default M4 output is HIGH ?!)

Other M4 pull-up/downs?

Also, consider switching to a bunch of resistor arrays for less things to place!

andrewgreenberg, 2021-02-14:
Fixed!

Closed 2021-02-14.

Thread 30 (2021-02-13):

TOT has pins switched

andrewgreenberg, 2021-02-13:
Looking over the TOT  part U24 the MAX941EUA+ ( comparator with a latch) the pin placement of the symbol was changed at some point and no longer matches the TOT simulation circuit as the LATCH is now connected to the - input where LATCH in both previous C3 versions and in the LTSpice TOT Simulation was connected to the + input of the (comparator with a latch).. in other words it looks like the symbol was "cleaned up" and the pins 2 and 3 flipped places but the connections to those pins did not get flipped.

andrewgreenberg, 2021-02-14:
Fixed.

Closed 2021-02-14.

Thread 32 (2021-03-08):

Unneeded PWRAMP net on L band

glennl, 2021-03-08:
The net between PWRAMP (AX5043 Pin 20) and JP2 - Pin 11 should be removed. It is not something likely ever to be used, and may cause problems if the shunt were installed and the pin programmed as an output. The default on power-up is input however.

Closed 2021-03-08.

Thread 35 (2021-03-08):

U15 (Qorvo/Triquint 856930) is obsolete and isn't in stock anywhere

andrewgreenberg, 2021-03-08:
We have 8 left; we can do two more runs of the C3 and then we're screwed. Please choose a new filter ASAP. Bonus points if it's a direct replacement, but I won't hold my breath :)

glennl, 2021-03-08:
This is a 457.5 MHz SAW filter.

glennl, 2023-11-19:
This component is special and we need to treat the ones we have like gold. I have not yet found a reasonable replacement. We can move to another IF frequency allowing us to use another available part, however this will require us to change the LO (synthesizer) frequency. This will require us to do an analysis of the new image frequencies that are formed by this. Vigely did extensive work with this, so we will need to go back to his thesis to review his process. It's totally doable, but not trivial.

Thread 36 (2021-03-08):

Add UHF reverse power detector test point

glennl, 2021-03-08:
Add a test point to the UHF reverse power detector.
Similar to TP10 on the forward power detector.

andrewgreenberg, 2022-12-30:
Done (TP29).

Closed 2022-12-30.

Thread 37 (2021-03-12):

Allow the M4 to power cycle the L band radio.

andrewgreenberg, 2021-03-12:
... rebooting that radio makes sense now and then, without power cycling the whole C3 card.

andrewgreenberg, 2022-12-30:
This is on hold for right now; don't want to add extra complexity.

andrewgreenberg, 2023-08-29:
Implemented in v6; the Octavo can now turn off power to both the L band and UHF radio AX5043 and associated circuitry.

Closed 2023-08-29.

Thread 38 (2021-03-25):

v5 WDT circuit wrong

andrewgreenberg, 2021-03-25:
Change R78, R32 to 3k.
Change R77, R76, R113 to 10k.
Add R25 (100k)  from 2IN+ (TP27) to VIN.

andrewgreenberg, 2021-03-25:
Fixed on C3 V5 #1; other boards need fixing and don't forget to update the BOM.

andrewgreenberg, 2022-12-29:
Done and confirmed. Closing.

Closed 2022-12-29.

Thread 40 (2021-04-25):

Add 10uF to VBUSP

oliver-rew, 2021-04-25:
Voltage dips on VBUS were browning out C3, so add 10uF on VBUSP close to the TPS6111

andrewgreenberg, 2022-12-30:
There was already one there, but I thought it wouldn't hurt to add one more, so done.

andrewgreenberg, 2022-12-30:
Also couldn't help myself, added another 10u to the output of the 3.3V switcher.

Closed 2022-12-30.

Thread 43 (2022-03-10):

Change R50 to 120 ohms

andrewgreenberg, 2022-03-10:
Causes LNA to be unconditionally stable, which should quell oscillations we see on v5 at low temperatures. Tradeoff: reduced gain and higher power consumption

andrewgreenberg, 2022-12-30:
This was before we found out about the lack of emitter generation on Q7; this should be resolved by re-implementing that. See also #44 and #47.

Closed 2022-12-30.

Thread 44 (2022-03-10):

Increase inductance to ground on Q7's emitter pins

andrewgreenberg, 2022-03-10:
This should increase stability by adding more inductance to Q7.

andrewgreenberg, 2022-12-30:
Duplicate of #44; just fixed by copying LEGO board layout's emitter degeneration.

Closed 2022-12-30.

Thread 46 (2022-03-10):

Move to v2 backplane (power connections, and UART to backplane)

andrewgreenberg, 2022-03-10:
Bring up to v2 backplane!

andrewgreenberg, 2022-12-29:
Done, except for C3-UART-TX/RX. This brings up an important point - should that be the CLI UART? or if we want a back channel to other cards, does that HAVE to be a difference UART? Maybe we can do both via GPIO tri-state control?

andrewgreenberg, 2022-12-29:
We're using USART3 for the CLI. Pins we have available that have UART alternate functions:
PA0 - 23 - UART4_TX
PA1 - 24 - UART4_RX
PA2 - 25 - USART2_TX
PA3 - 26 - USART2_RX
PC6 - 63 - USART6_TX
PC7 - 64 - USART6_RX

Free pins that don't do UARTs: PB0, PB1, PB2, PC13, PD14, PD15, PE4, PE5, PE6, PE9

andrewgreenberg, 2022-12-30:
Connected up USART6; waiting for firmware folks to OK.

andrewgreenberg, 2023-08-29:
No longer relevant for the v6 since we switched to the Octavo.

Closed 2023-08-29.

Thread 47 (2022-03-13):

Important: Add PCB inductance between Q7 emitter and ground

glennl, 2022-03-13:
There is a needed inductance formed by traces on the PCB between the two emitter pins of Q7, and the surrounding ground plane. This inductance is very small, but essential as a form of regeneration to maintain stability. The inductance was provided on the dev boards, but was incorrectly changed as far back as v3. There was a fix applied to v5 boards by trimming away part of the PCB trace, and that confirmed its requirement, as shown in testing that the LNA breaks into oscillation when temperature is at or below room temp.

The trace inductor needs to correctly be applied to the board, and indicated on the schematic using an inductor symbol, and noted that it is formed by a PCB trace of some specified dimensions.

glennl, 2022-12-28:
This may be the same as issue #44?

andrewgreenberg, 2022-12-30:
Added emitter degenerattion like the "LEGO" board. Moving other components next door since we have more room now.

Closed 2022-12-30.

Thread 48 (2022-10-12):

Investigate AX5043 RX/TX matching circuit at UHF radio

zisi, 2022-10-12:
Hi, i would like to ask about the matching circuit in balanced and unbalanced lines in the AX5043. In both cases at 436.5MHz your design is different for the proposed design in [datasheet](https://www.onsemi.com/pdf/datasheet/ax5043-d.pdf). How you calculate these L-C values?
For example in TX the C65 and L139 and in RX the BaLun L11,C58,C59 and L10(+L12), how you calculate, which is the input/output impedance of AX5043 at ~430MHz?

Thanks

zisi, 2022-10-14:
According to [this](https://www.onsemi.com/forum/t/faq-how-to-operate-ax5043-at-27-mhz-custom-matching-networks-for-ax5043/274/7), i understand that you do not need the load network for internal differential PA, because you use the differential path only as RX, like this [application note](https://www.onsemi.com/download/application-notes/pdf/and9312-d.pdf). So you need only a BalUn, with input balanced impedance 100Ohm to unbalanced 50Ohm. I'm not sure about the usage of L12.

zisi, 2022-10-25:
Hi, there: https://gitlab.com/librespacefoundation/pq9ish/pq9ish-comms-vu-hw/-/issues/6#note_1141997003 you can find an analysis to reduce parts for RX and TX paths. I think we can close the issue.

Thanks to have your project open and share your knowledge about RF.

andrewgreenberg, 2023-08-29:
OK! Closing!

Closed 2023-08-29.

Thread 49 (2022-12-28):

Update Readme page

glennl, 2022-12-28:
The current page describes current status as _OreSat C3 version 4_; we need to get past v5, and now onto V6.

andrewgreenberg, 2022-12-30:
Fixed!

Closed 2022-12-30.

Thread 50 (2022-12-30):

UHF receive sensitive is 15 db down from expected

andrewgreenberg, 2022-12-30:
... why?

andrewgreenberg, 2023-08-29:
We found out that the previous UHF LNA based on the BFPXXXF did _not_ like going into a high impedance. It wouldn't actually put out 21 dB without some kind of 50 ohm load on the output. This was.. unexpected. Since we already switched to the TQP3M9036 for the L band, we decided to switch the UHF LNA to the same IC. It burns power, but it should be stable and give us the gain we expect.

Closed 2023-08-29.

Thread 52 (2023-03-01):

Add specialized RF test points for easy probing

andrewgreenberg, 2023-03-01:
Come up with a common spacing for SMT pad (0.38 mm wide so it doesn't affect the trace) and a ground pin for both the RF probe and regular scope probes.

glennl, 2023-03-26:
At these test points point, it is expected that UT-047 semi rigid coax is to be attached. There is a pre-formed product from DigiKey ([931-1391-ND](https://www.digikey.com/en/products/detail/taoglas-limited/CAB-058/5287277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)) to implement this.

andrewgreenberg, 2023-08-29:
This is done; See new "mask only" TPs meant to be overlayed on the RF trace. There are two FAB circles for putting GND vias, and then the GND - signal - GND spacing of 1 mm nicely allows for probing with this test probe: https://www.ebay.com/itm/185381060789

Closed 2023-08-29.

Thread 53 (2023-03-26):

Replace 3rd order BPF following LNA with SAW

glennl, 2023-03-26:
Replace the 3rd order BPF **_following LNA_** with a SAW filter device for better performance and better impedance matching.

Remove;
L29, 30, 31
C108, 109, 110

Use in it's place;
SF2446E
https://www.mouser.com/datasheet/2/1100/sf2446e-1917649.pdf

glennl, 2023-03-27:
Possibly consider changing the first 3rd order BPF also?

L26, 27, 28
C96, 101, 107

cesarordaz, 2023-05-21:
Replaced both

Closed 2023-05-21.

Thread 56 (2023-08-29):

Move components away from +/- Y edges to enable placement under frame bosses

andrewgreenberg, 2023-08-29:
In the rush to get to the v6, we put components next to the Y edges of the board, under where the frame bosses go if you're flying a 1U. This won't impact OreSat0.5 or Oresat1, but it will impact future 1U CubeSats.

Move components away from the Y edges to the point that C3 v6 card can be inserted underneath the top 1U frame boss.

andrewgreenberg, 2024-02-29:
Specifically, the only component left that prevents a card slot next to a boss is now C132.

andrewgreenberg, 2024-04-09:
This was done for v6.1!

Closed 2024-04-09.

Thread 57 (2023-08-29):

U34 I_LIM could go to A8 ADC to monitor current consumption

andrewgreenberg, 2023-08-29:
The C3 v6 could be monitoring its own current usage if we hooked up U34's I_LIM pin and resistor to the last remaining Octavo ADC port. That'll be a bit hairy to lay out, which is why it's not done on the v6.0.

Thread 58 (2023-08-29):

Are the 220 uF Tantalums for the watchdog sealed?

andrewgreenberg, 2023-08-29:
We were warned that Tantalums can "leak" in a vacuum and basically die as an open. Not sure if your 220 uF caps are sealed, or if they have this problem. Investigate! And if we're paranoid, switch to a bunch of ceramics.

Also, measure the life time of the watchdog on the capacitors; we might not need anywhere near that amount.

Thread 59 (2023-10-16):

Fix brown out on radio enable

andrewgreenberg, 2023-10-16:
When turning on v6.0 radio power, the Octavo resets due to a brown out.

- Change the dv/dt resistor of the TPS, or change it back (see cesar's changes)
- Add more capacitance on the input of the system (C6) - maybe double
- Add more caps to the VIN_AC - maybe double
- Add individual enable lines to 3.3V LDOs from GPMC_A0 to UHF and GPMC_A3 to L BAND.
-

andrewgreenberg, 2023-11-13:
Connected 3.3V LDO enables. Also look into more caps and the TPS's dv/dt.

andrewgreenberg, 2023-12-21:
Separate enable lines added on the LDOs.
Added 22 uF added to VBUS.
Added 22 uF to VIN_AC.
TPS capacitor didn't help, still browned out, because the LTC kicks in after the initial voltage ramp up.

Closed 2023-12-21.

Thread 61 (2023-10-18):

RXTX switch U20 needs better EN/CTRL voltages

andrewgreenberg, 2023-10-18:
Data sheet says > 2.75 but < 3.0, and we're giving it 1.8V, so it's not actually turning on. Why in the world did this work for the v5?!

andrewgreenberg, 2023-10-18:
Used 1k and 6.8k, for  R14, R15 which worked great (~ 2.85 V), but try to choose values that are already being used. Also, update R13, R16.

andrewgreenberg, 2023-11-13:
In 6.1, switched to 3k/22k, which gives 2.9V which is > 2.8Vhi max and < 3.0 Vmax.

Closed 2023-11-13.

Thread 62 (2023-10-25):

UHF TX 5th order LPF dropping 6 dBm

andrewgreenberg, 2023-10-25:
Either replace with values from 2023-10-24 testing (see #oresat-comms), or replace with some solid state device.

andrewgreenberg, 2023-11-13:
OK I've updated this to: L17, L18 are 18nH, and C87 = 3pF, C86 = 8.3 pF, and C85 = 3pF.

Close this issue if you want to stick with this, otherwise let me know better values and/or a good IC.

glennl, 2023-11-19:
Let;s keep this as is.
Rationale:
The components chosen gives a break frequency of around 700 MHz, which keeps the the passband S21 around -0.15 dB, and the first harmonic (which is what we want to supress) at 900 MHz with S21 around -10.5 dB. The insertion loss of 6 dB is the voltage loss, and power loss is 3 dB. This is expected, and SAW devices are not much better for overall S21. SAW's shine with steep skirts, but we are okay with this.

glennl, 2023-11-19:
Let's keep this as is.
Rationale:
The components chosen gives a break frequency of around 700 MHz, which keeps the the passband S21 around -0.15 dB, and the first harmonic (which is what we want to supress) at 900 MHz with S21 around -10.5 dB. The insertion loss of 6 dB is the voltage loss, and power loss is 3 dB, which is expected. SAW devices are not much better for overall S21. SAW's shine with steep skirts, but we are okay with this response.

Closed 2023-11-19.

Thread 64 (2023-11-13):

OK to change R109 to 22k?

andrewgreenberg, 2023-11-13:
I'd like to change R109 from 15k to 22k. This means the TOT voltage will rise from 0.43V to 0.60V. Is that OK? We'd get to save a whole resistor value, which would be nice.

glennl, 2023-11-19:
I strongly vote no, since this will require a higher power level to qualify the transmission as a valid power level for the watchdog. This will require testing to confirm an acceptable power range. If only to simplify parts inventory, it's not worth it.

Closed 2023-11-19.

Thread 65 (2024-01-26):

Rework UHF transmit power annotations

glennl, 2024-01-26:
The UHF transmit power annotation are essentially correct, however the PA cannot put out more than +30 dBm. The values shown were adjusted form actual lower power measurements.

glennl, 2024-02-29:
Measured values taken today (28-Feb-2024). We did not measure at points TP908 or TP905, so those annotations have been removed.

Closed 2024-02-29.

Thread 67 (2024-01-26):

Consider a new UHF transmit PA device

glennl, 2024-01-26:
The existing UHF transmit power amplifier (PA) device since the current device has gone to end of life.

andrewgreenberg, 2024-02-29:
This is now an enhancement; we're going with the current PA for OreSat0.5 and Oresat1.

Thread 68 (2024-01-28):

Investigate Octavo not booting up on every power reset

andrewgreenberg, 2024-01-28:
Usually seen in C3 power up. PB sometimes doesn't boot up, either.

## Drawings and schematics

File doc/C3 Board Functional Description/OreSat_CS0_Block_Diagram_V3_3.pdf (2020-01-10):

## Critical Subsystem

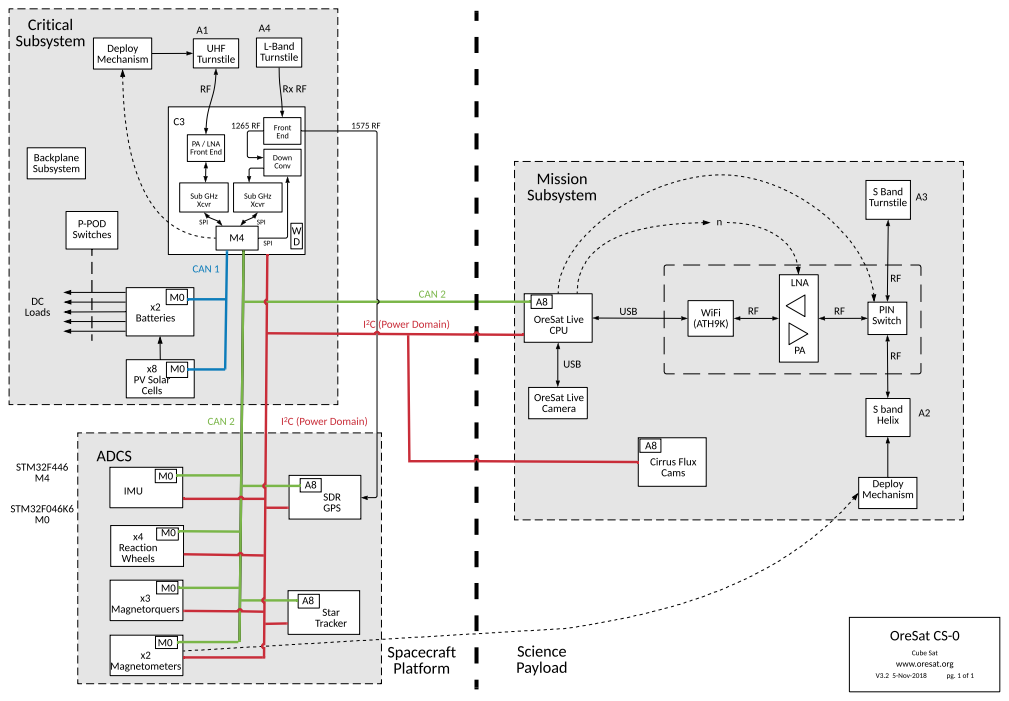
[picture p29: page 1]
OreSat CS-0; V3.2 5-Nov-2018; LNA; CAN 2; STM32F446 M4; STM32F046K6 M0; UHF Turnstile; Deploy Mechanism; P-POD Switches; x2 Batteries; x8 PVSolar Cells; SPI; DC Loads; IMU; x2 Magnetometers; SBand Turnstile; OreSat Live Camera; PIN Switch; SDR GPS; Sband Helix; OreSat Live CPU; WiFi (ATH9K); Spacecraft Platform; Science Payload; USB; L-Band Turnstile; Down Conv; Sub GHz Xcvr; PA/ LNA Front End; Front End; Backplane Subsystem; CAN 1; Star Tracker; CAN2; M0 x4 Reaction Wheels; x3 Magnetorquers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

I²C(Power Domain)

Cube Sat
www.oresat.org

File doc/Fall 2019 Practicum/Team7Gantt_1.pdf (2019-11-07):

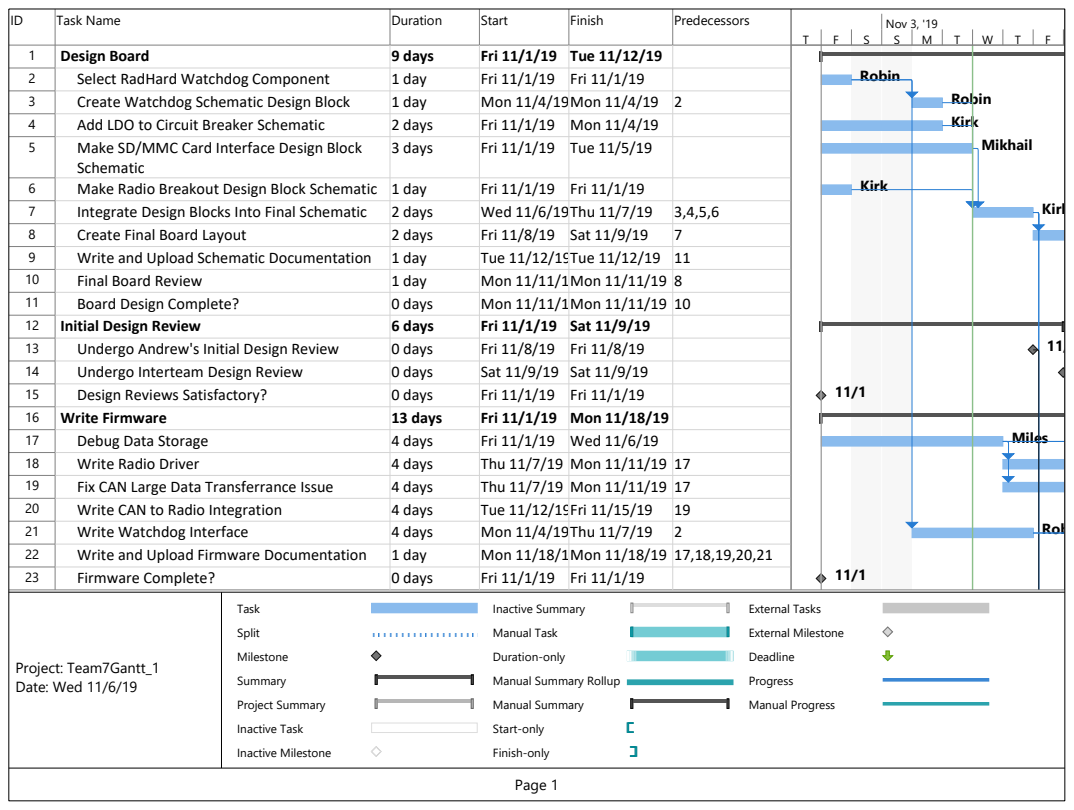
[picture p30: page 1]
Task Name; Duration; Start; Finish; Predecessors; Design Board; 9 days; Fri 11/1/19; Tue 11/12/19; Select RadHard Watchdog Component; 1 day; Create Watchdog Schematic Design Block; Mon 11/4/19Mon 11/4/19; Add LDO to Circuit Breaker Schematic; 2 days; Mon 11/4/19; Make SD/MMC Card Interface Design Block; Schematic; 3 days; Tue 11/5/19; Make Radio Breakout Design Block Schematic; Integrate Design Blocks Into Final Schematic; Wed 11/6/19Thu 11/7/19; Create Final Board Layout; Fri 11/8/19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

Manual Summary Rollup

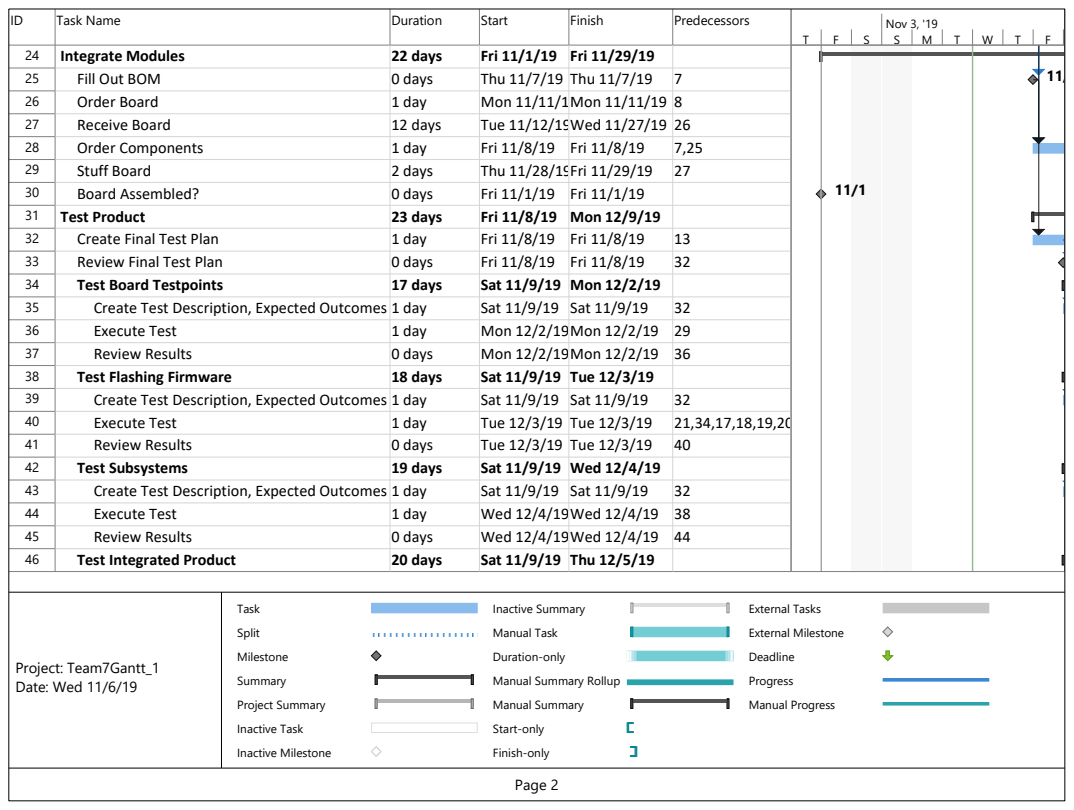
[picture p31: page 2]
Integrate Modules; 22 days; Fri 11/1/19; Fri 11/29/19; Fill Out BOM; 0 days; Thu 11/7/19; Order Board; 1 day; Mon 11/11/19Mon 11/11/19; Receive Board; 12 days; Tue 11/12/19Wed 11/27/19; Order Components; Fri 11/8/19; Stuff Board; 2 days; Thu 11/28/19Fri 11/29/19; Board Assembled?; Test Product; 23 days; Mon 12/9/19; Create Final Test Plan; Review Final Test Plan; Test Board Testpoints; 17 days; Sat 11/9/19; Mon 12/2/19; Create Test Description, Expected Outcomes 1 day; Execute Test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

Manual Summary Rollup

47 | Create Test Description, Expected Outcomes 1 day | Sat 11/9/19 | Sat 11/9/19 | 32
48 | Execute Test | 1 day | Thu 12/5/19 | Thu 12/5/19 | 42
49 | Review Results | 0 days | Thu 12/5/19 | Thu 12/5/19 | 48
50 | Review Final Test Results | 1 day | Fri 12/6/19 | Fri 12/6/19 | 46
51 | Check Performance Against Requirements | 1 day | Fri 12/6/19 | Fri 12/6/19 | 46
52 | Discuss Revision of Design | 1 day | Mon 12/9/19Mon 12/9/19 | 50
53 | Document Test Results | 1 day | Mon 12/9/19Mon 12/9/19 | 50
54 | Project Development Complete? | 0 days | Mon 12/9/19Mon 12/9/19 | 52
55 | Market and Sell Product | 3 days | Fri 12/6/19 | Tue 12/10/19
56 | Create Powerpoint Slide(General) | 2 days | Fri 12/6/19 | Mon 12/9/19 | 46
57 | Review Powerpoint | 0 days | Mon 12/9/19Mon 12/9/19 | 56
58 | Rehearse Presentation | 0 days | Mon 12/9/19Mon 12/9/19 | 56
59 | Present Project(General) | 1 day | Tue 12/10/19Tue 12/10/19 | 56
60 | Project Complete? | 0 days | Tue 12/10/19Tue 12/10/19 | 59
T | F | S | S | M | T | W | T | F

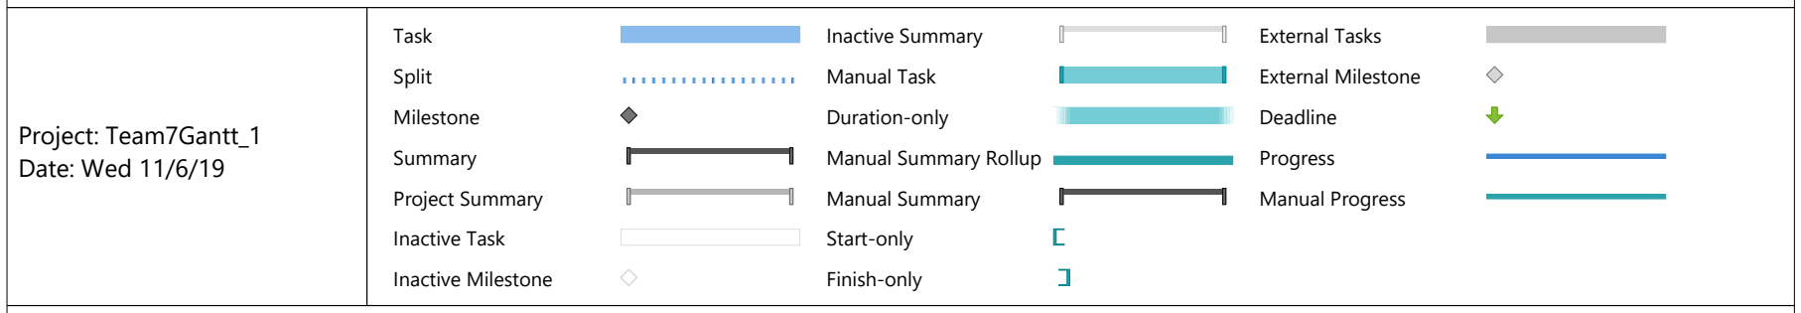
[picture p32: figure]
Task; Split; Milestone; Summary; Project Summary; Inactive Task; Inactive Milestone; Inactive Summary; Manual Task; Duration-only; Manual Summary Rollup; Manual Summary; Start-only; Finish-only; External Tasks; External Milestone; Deadline; Progress; Manual Progress; Project: Team7Gantt_1 Date: Wed 11/6/19
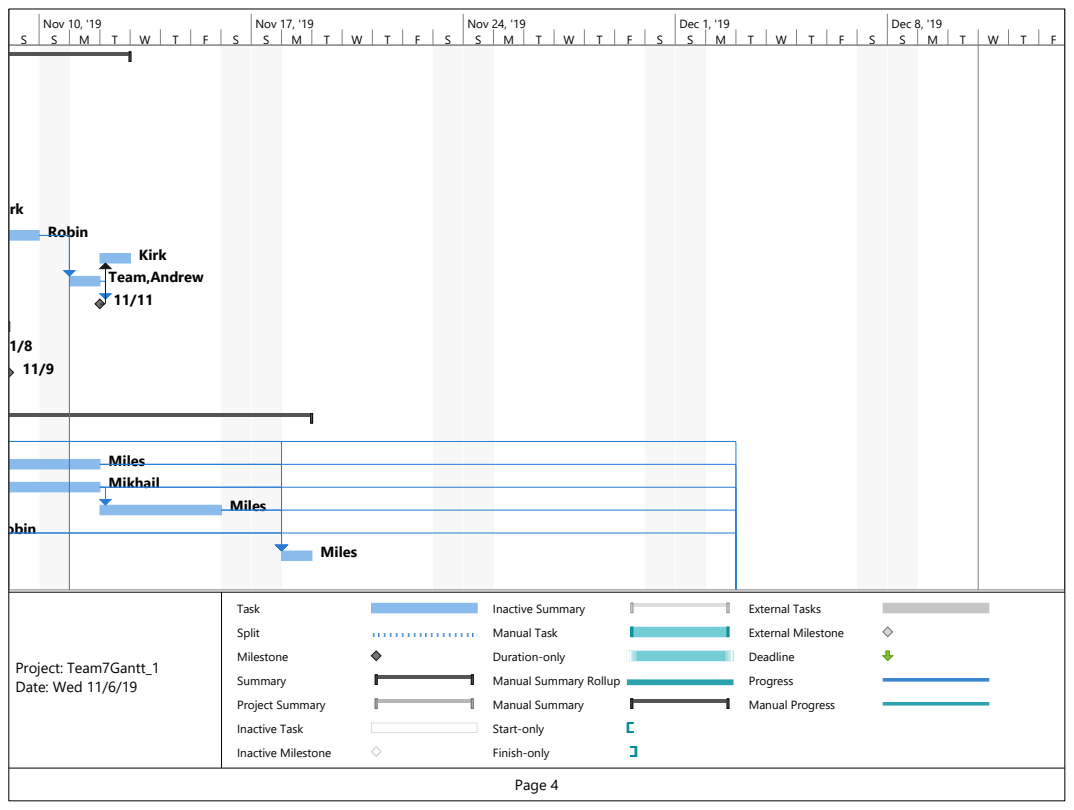
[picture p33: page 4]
Mikhail; Kirk; Robin; Team,Andrew; Miles; Nov 10, '19; Nov 17, '19; Nov 24, '19; Dec 1, '19; Dec 8, '19; Task; Split; Milestone; Summary; Project Summary; Inactive Task; Inactive Milestone; Inactive Summary; Manual Task; Duration-only; Manual Summary; Start-only; Finish-only; External Tasks; External Milestone; Deadline; Progress; Manual Progress; Project: Team7Gantt_1 Date: Wed 11/6/19

Manual Summary Rollup

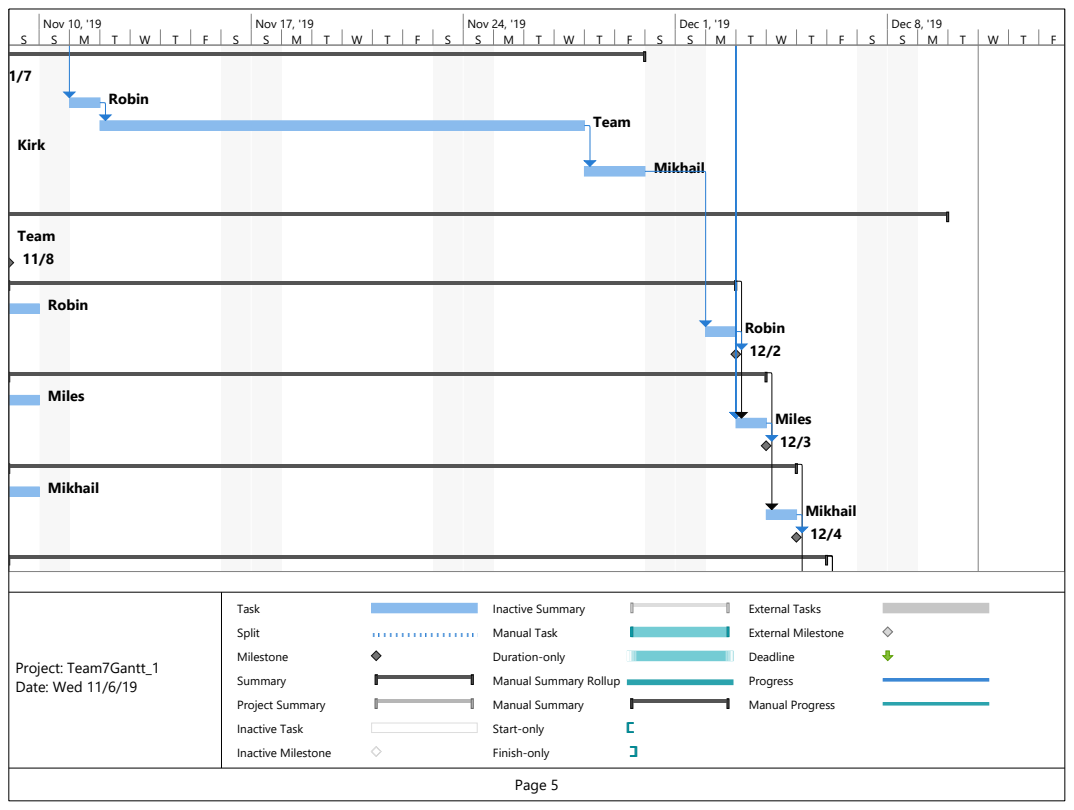
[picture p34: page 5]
Robin; Miles; Mikhail; Task; Split; Milestone; Summary; Project Summary; Inactive Task; Inactive Milestone; Inactive Summary; Manual Task; Duration-only; Manual Summary; Start-only; Finish-only; External Tasks; External Milestone; Deadline; Progress; Manual Progress; Project: Team7Gantt_1 Date: Wed 11/6/19

Kirk Team 11/8 | Robin | Team Mikhail

Robin

Miles

Mikhail

Manual Summary Rollup

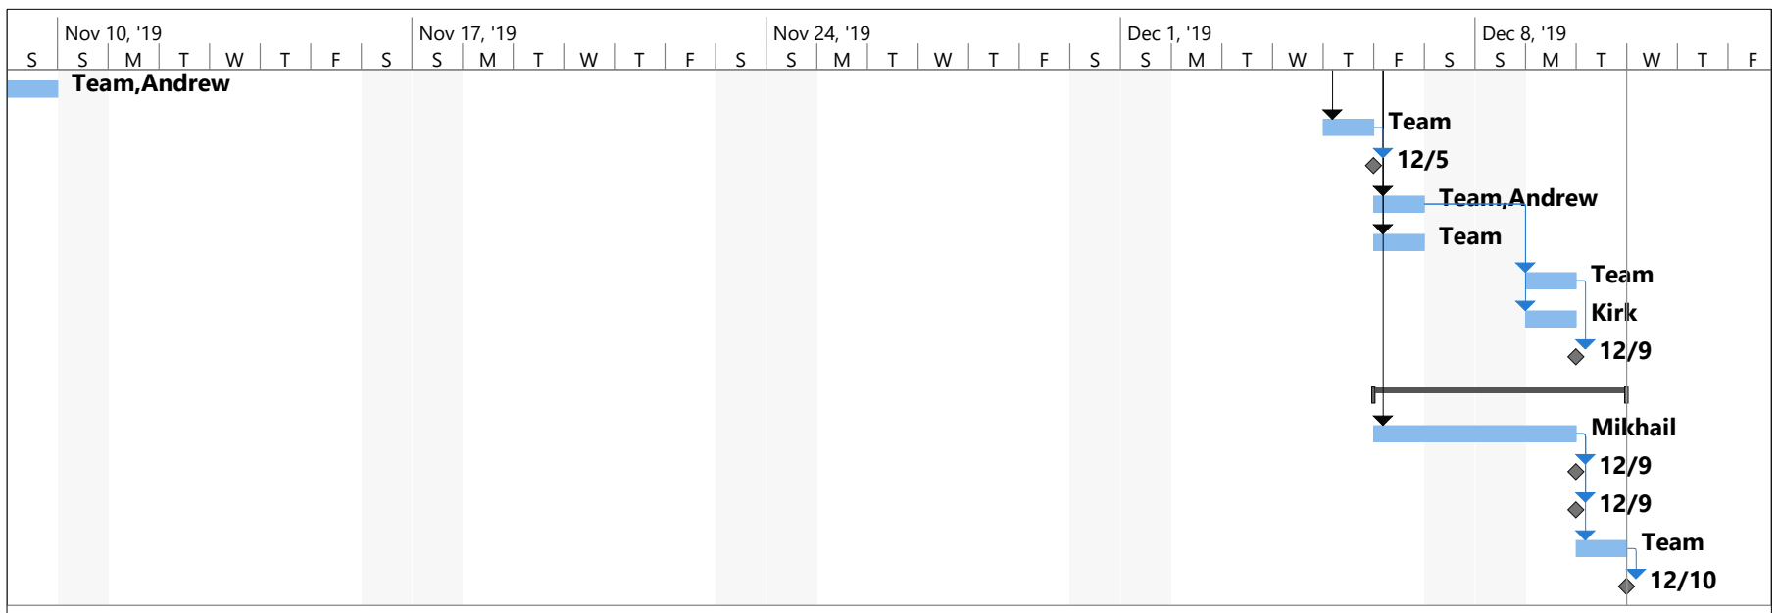
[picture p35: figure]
Team,Andrew; Team; Kirk; Mikhail

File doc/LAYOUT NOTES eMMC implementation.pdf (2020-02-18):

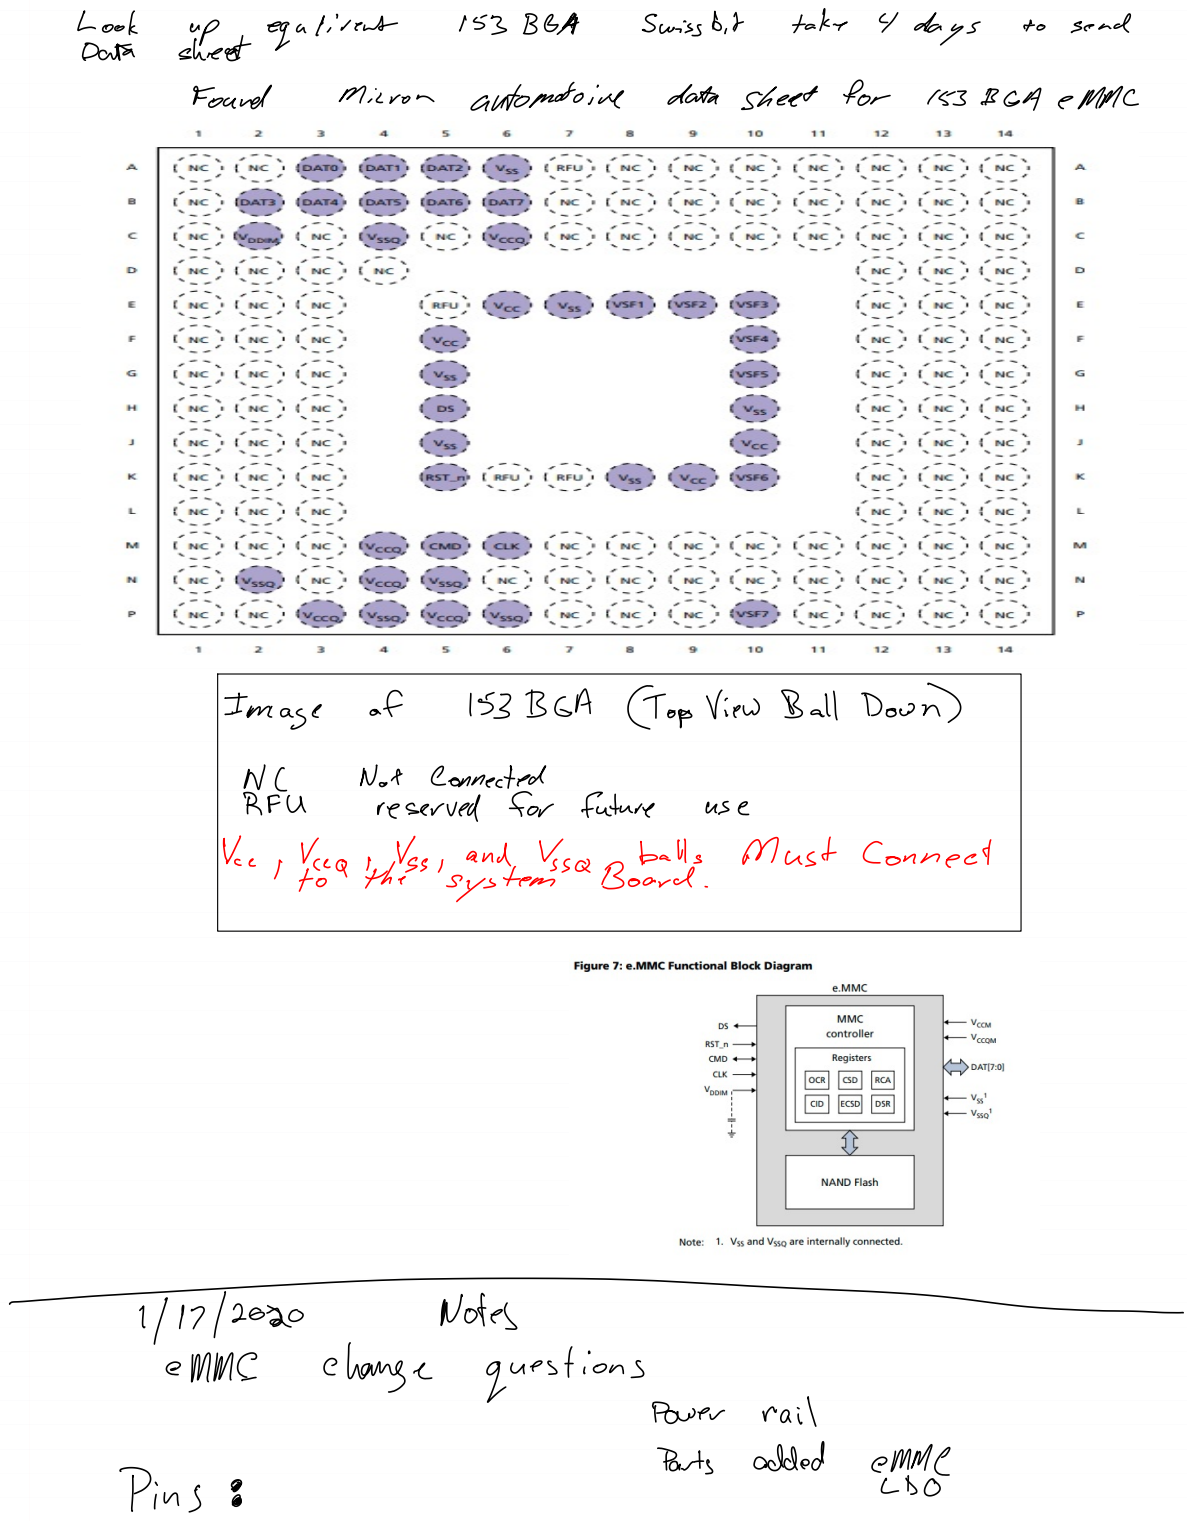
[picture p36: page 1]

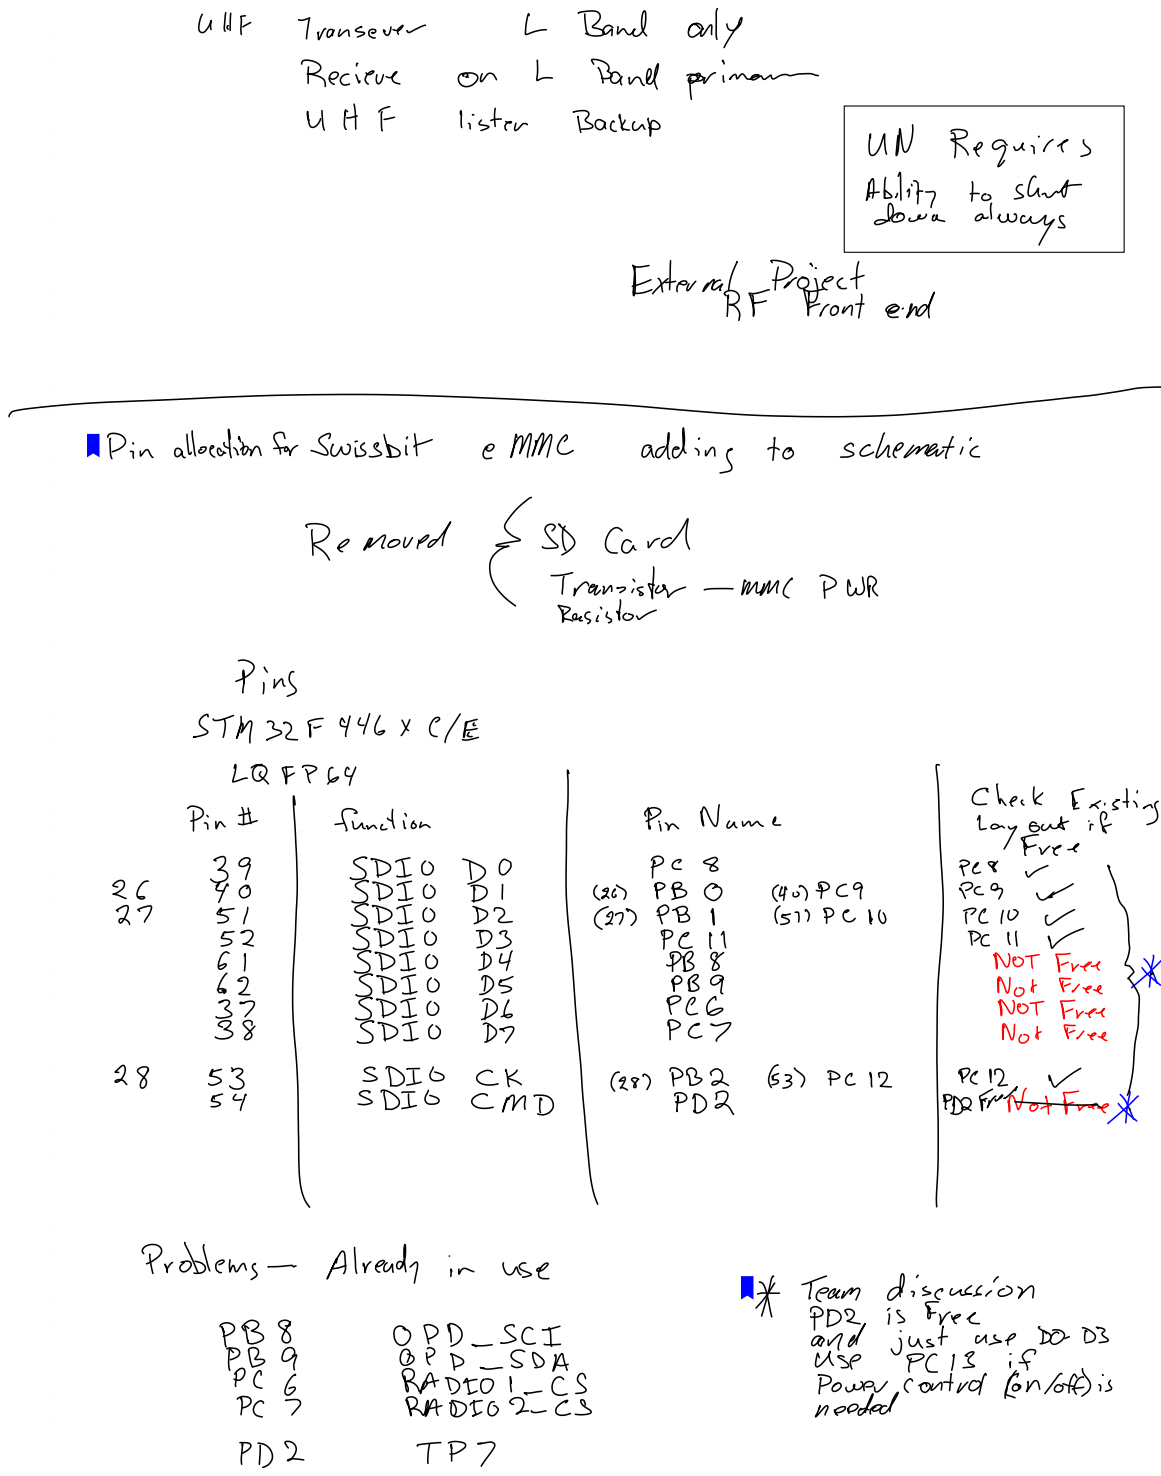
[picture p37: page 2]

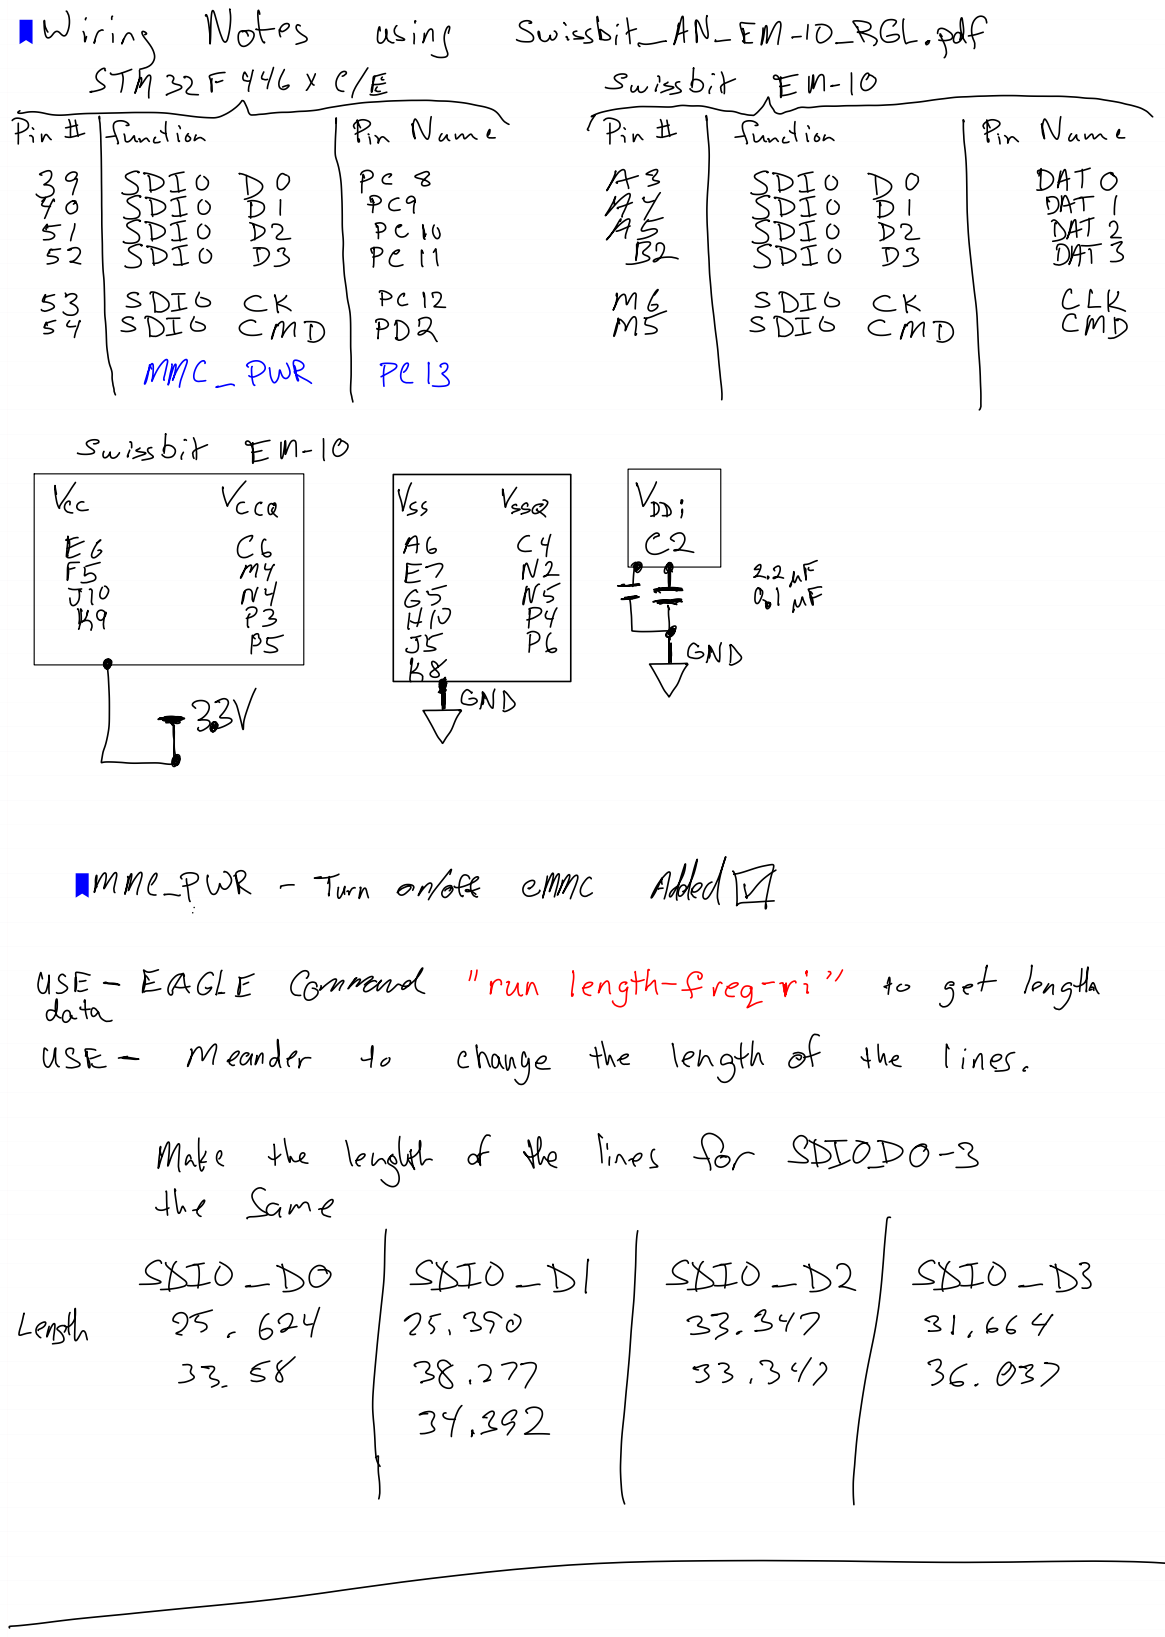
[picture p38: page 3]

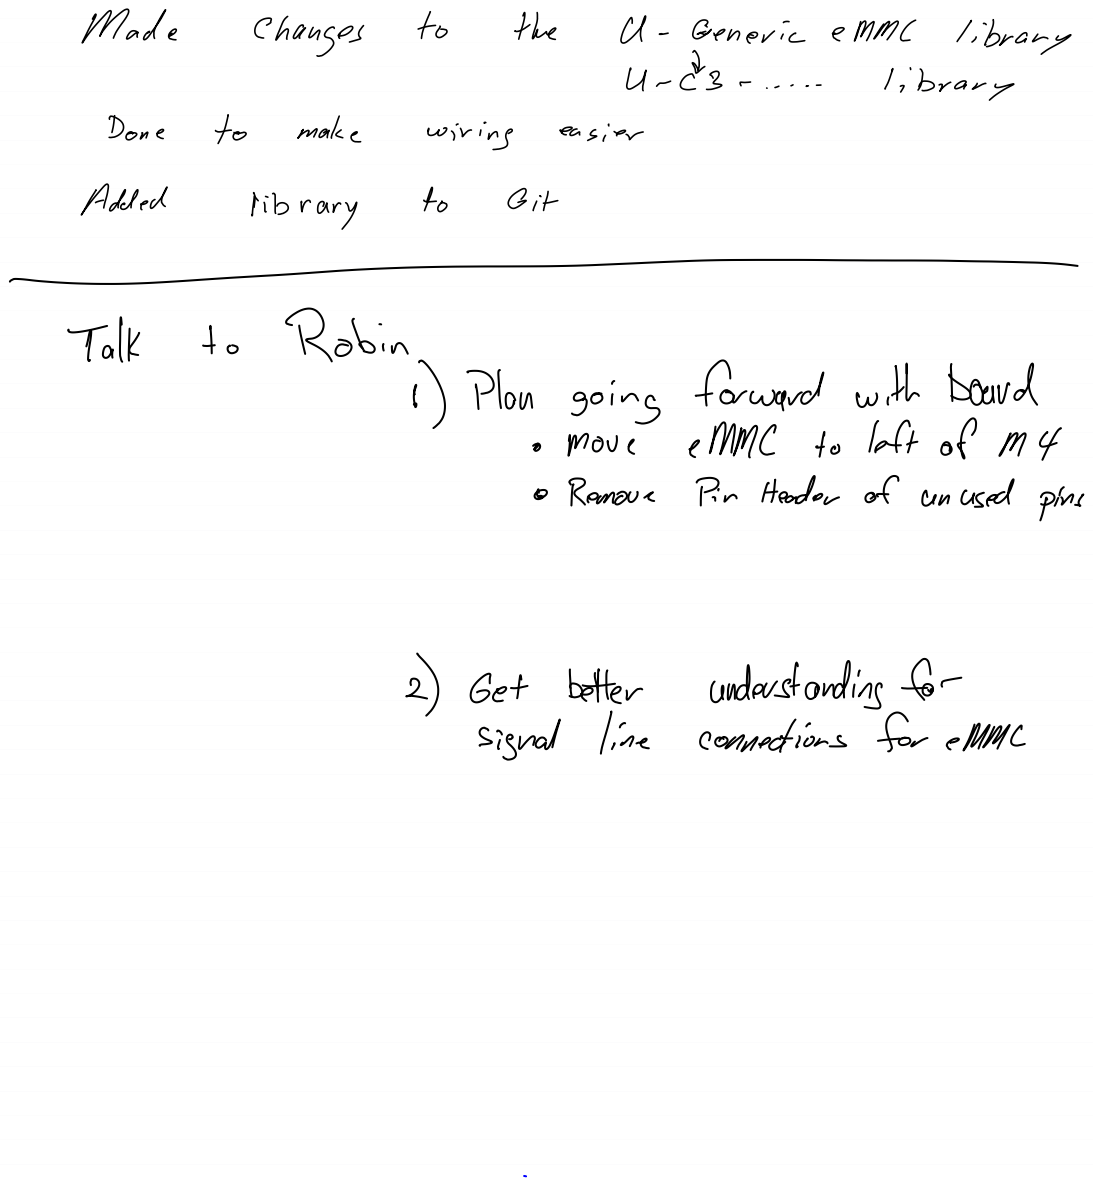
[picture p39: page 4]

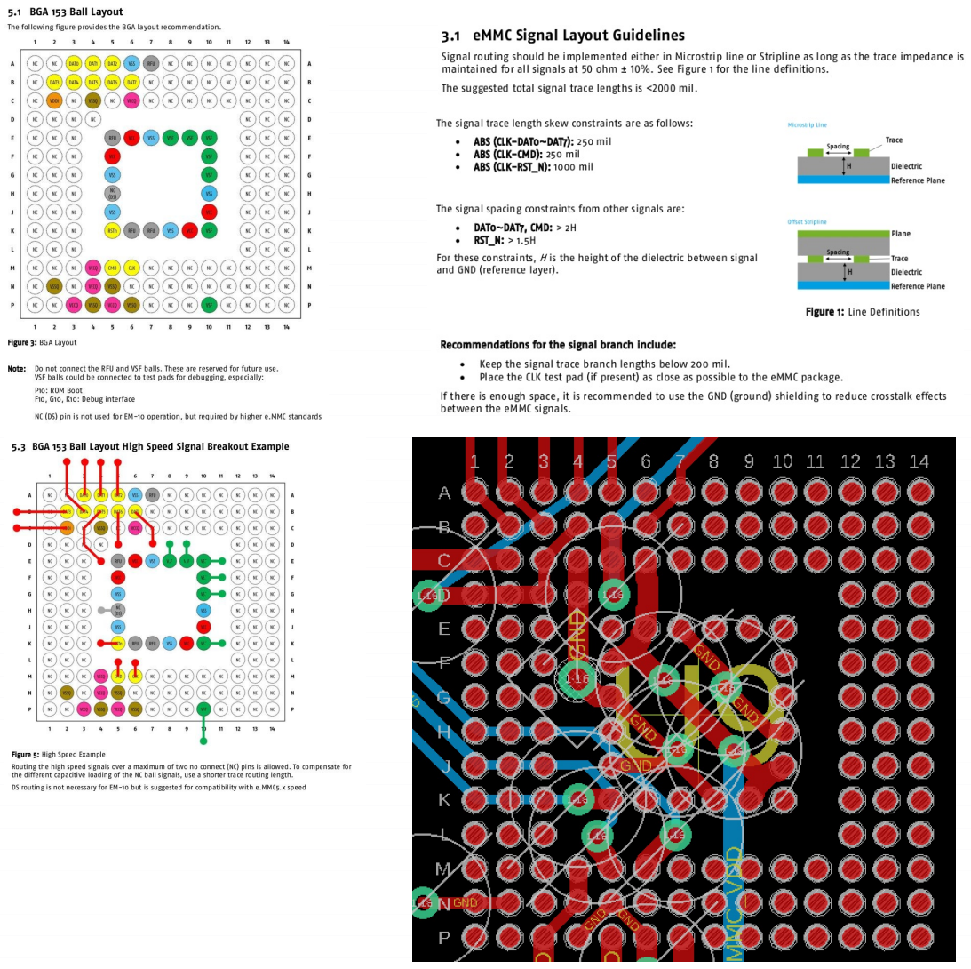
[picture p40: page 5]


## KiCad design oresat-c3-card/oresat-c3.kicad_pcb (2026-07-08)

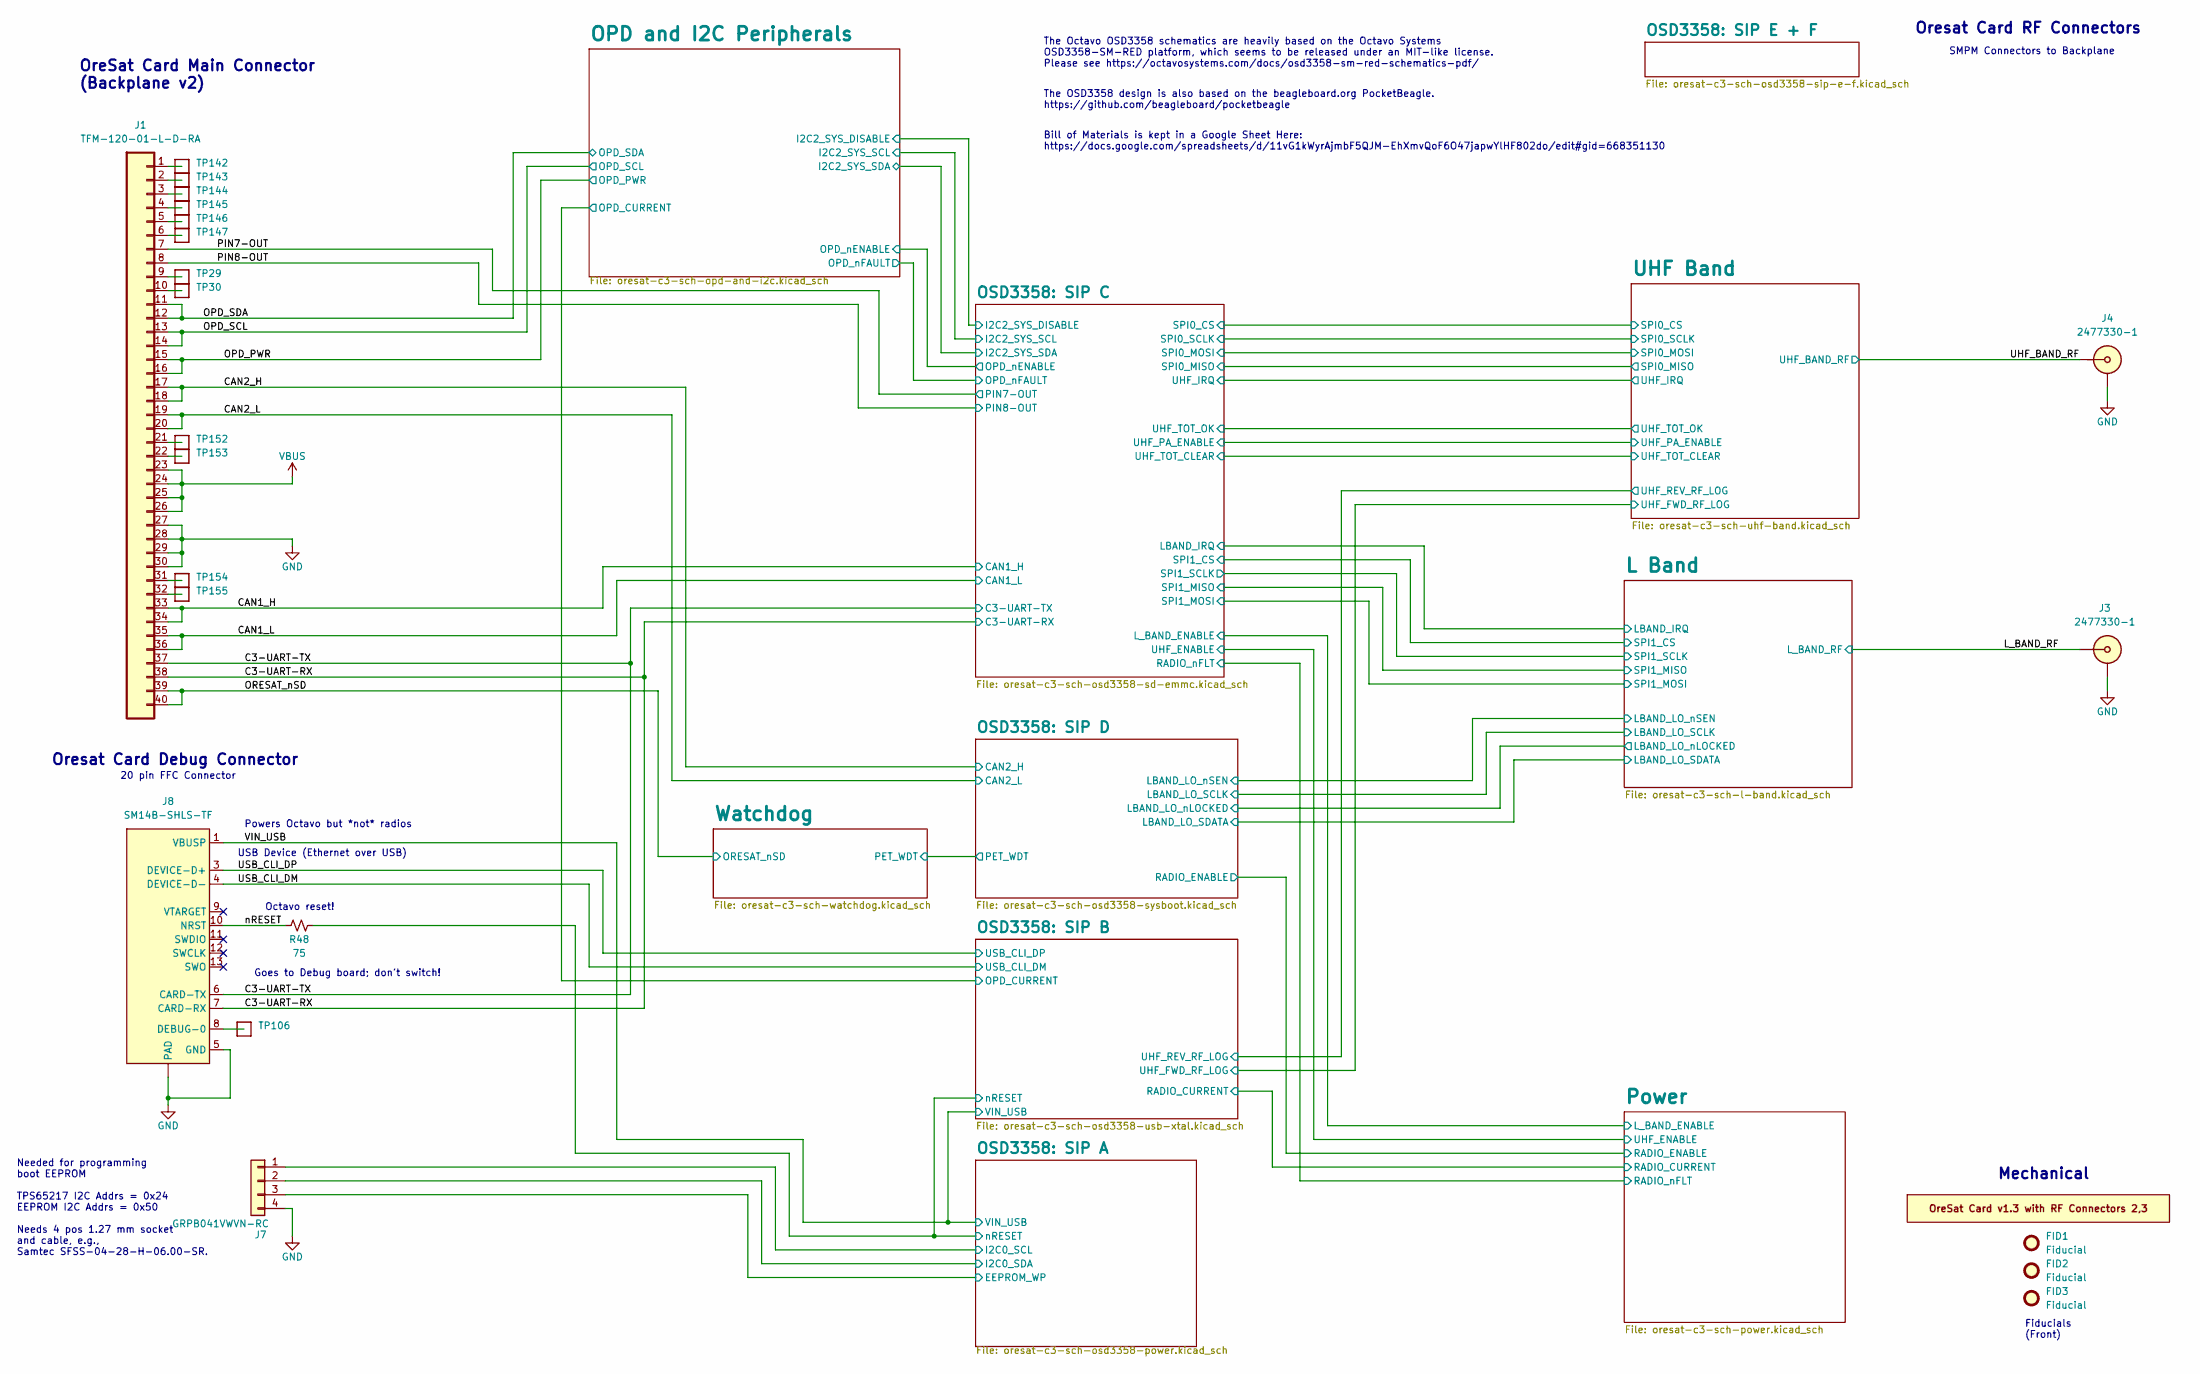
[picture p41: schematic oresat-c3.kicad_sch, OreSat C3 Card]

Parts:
FID1, FID2, FID3: Fiducial; Fiducial_1mm_Mask2mm
J1: TFM-120-01-L-D-RA; J-SAMTEC-TFM-120-X1-XXX-D-RA; MPN TFM-120-01-L-D-RA
J3, J4: 2477330-1; J-MOLEX-SMPM-073300-002X; MPN 2477330-1
J7: GRPB041VWVN-RC; PinHeader_1x04_P1.27mm_Vertical; MPN GRPB041VWVN-RC
J8: SM14B-SHLS-TF; J-JST-SM14BSHLSTF; MPN SM14B-SHLS-TF
PCB1: ORESAT-CARD-V1.3-GENERIC-1RF-POS2; ORESAT-CARD-V1.3-2RF-RIGHT; MPN N/A
R48: 75; 0603-C-NOSILK; MPN RMCF0603FT75R0
TP29, TP30, TP106, TP142, TP143, TP144, TP145, TP146, TP147, TP152, TP153, TP154, TP155: Test-Point; TestPoint_Pad_D1.0mm

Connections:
/C3-UART-RX: J1.38, J8.7 (CARD-RX); also elsewhere on the board
/C3-UART-TX: J1.37, J8.6 (CARD-TX); also elsewhere on the board
/CAN1_H: J1.33, J1.34; also elsewhere on the board
/CAN1_L: J1.35, J1.36; also elsewhere on the board
/CAN2_H: J1.17, J1.18; also elsewhere on the board
/CAN2_L: J1.19, J1.20; also elsewhere on the board
/L_BAND_RF: J3.1 (SIG_SIG); also elsewhere on the board
/OPD_PWR: J1.15, J1.16; also elsewhere on the board
/OPD_SCL: J1.13, J1.14; also elsewhere on the board
/OPD_SDA: J1.11, J1.12; also elsewhere on the board
/ORESAT_nSD: J1.39, J1.40; also elsewhere on the board
/OSD3358: SIP A/EEPROM_WP: J7.3; also elsewhere on the board
/OSD3358: SIP A/I2C0_SCL: J7.1; also elsewhere on the board
/OSD3358: SIP A/I2C0_SDA: J7.2; also elsewhere on the board
/OSD3358: SIP A/nRESET: R48.2; also elsewhere on the board
/PIN7-OUT: J1.7; also elsewhere on the board
/PIN8-OUT: J1.8; also elsewhere on the board
/UHF_BAND_RF: J4.1 (SIG_SIG); also elsewhere on the board
/USB_CLI_DM: J8.4 (DEVICE-D-); also elsewhere on the board
/USB_CLI_DP: J8.3 (DEVICE-D+); also elsewhere on the board
/VIN_USB: J8.1 (VBUSP), J8.2 (VBUSP); also elsewhere on the board
/nRESET: J8.10 (NRST), R48.1
GND: J1.27, J1.28, J1.29, J1.30, J3.2 (SHLD_SHLD), J3.SHLD, J4.2 (SHLD_SHLD), J4.SHLD, J7.4, J8.5 (GND), J8.14 (GND), J8.15 (PAD), J8.16 (PAD); also elsewhere on the board
unnamed: J1.1, TP142.1 (1_1)
unnamed: J1.2, TP143.1 (1_1)
unnamed: J1.3, TP144.1 (1_1)
unnamed: J1.4, TP145.1 (1_1)
unnamed: J1.5, TP146.1 (1_1)
unnamed: J1.6, TP147.1 (1_1)
unnamed: J1.9, TP29.1 (1_1)
unnamed: J1.10, TP30.1 (1_1)
unnamed: J1.21, TP152.1 (1_1)
unnamed: J1.22, TP153.1 (1_1)
unnamed: J1.31, TP154.1 (1_1)
unnamed: J1.32, TP155.1 (1_1)
unnamed: J8.8 (DEBUG-0), TP106.1 (1_1)
VBUS: J1.23, J1.24, J1.25, J1.26; also elsewhere on the board

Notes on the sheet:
Bill of Materials is kept in a Google Sheet Here: https://docs.google.com/spreadsheets/d/11vG1kWyrAjmbF5QJM-EhXmvQoF6O47japwYlHF802do/edit#gid=668351130
The Octavo OSD3358 schematics are heavily based on the Octavo Systems OSD3358-SM-RED platform, which seems to be released under an MIT-like license. Please see https://octavosystems.com/docs/osd3358-sm-red-schematics-pdf/
OreSat Card Main Connector (Backplane v2)
Mechanical
Needed for programming boot EEPROM TPS65217 I2C Addrs = 0x24 EEPROM I2C Addrs = 0x50 Needs 4 pos 1.27 mm socket and cable, e.g., Samtec SFSS-04-28-H-06.00-SR.
Octavo reset!
20 pin FFC Connector
Oresat Card RF Connectors
Oresat Card Debug Connector
Goes to Debug board; don't switch!
Powers Octavo but *not* radios
The OSD3358 design is also based on the beagleboard.org PocketBeagle. https://github.com/beagleboard/pocketbeagle
USB Device (Ethernet over USB)
SMPM Connectors to Backplane
Fiducials (Front)

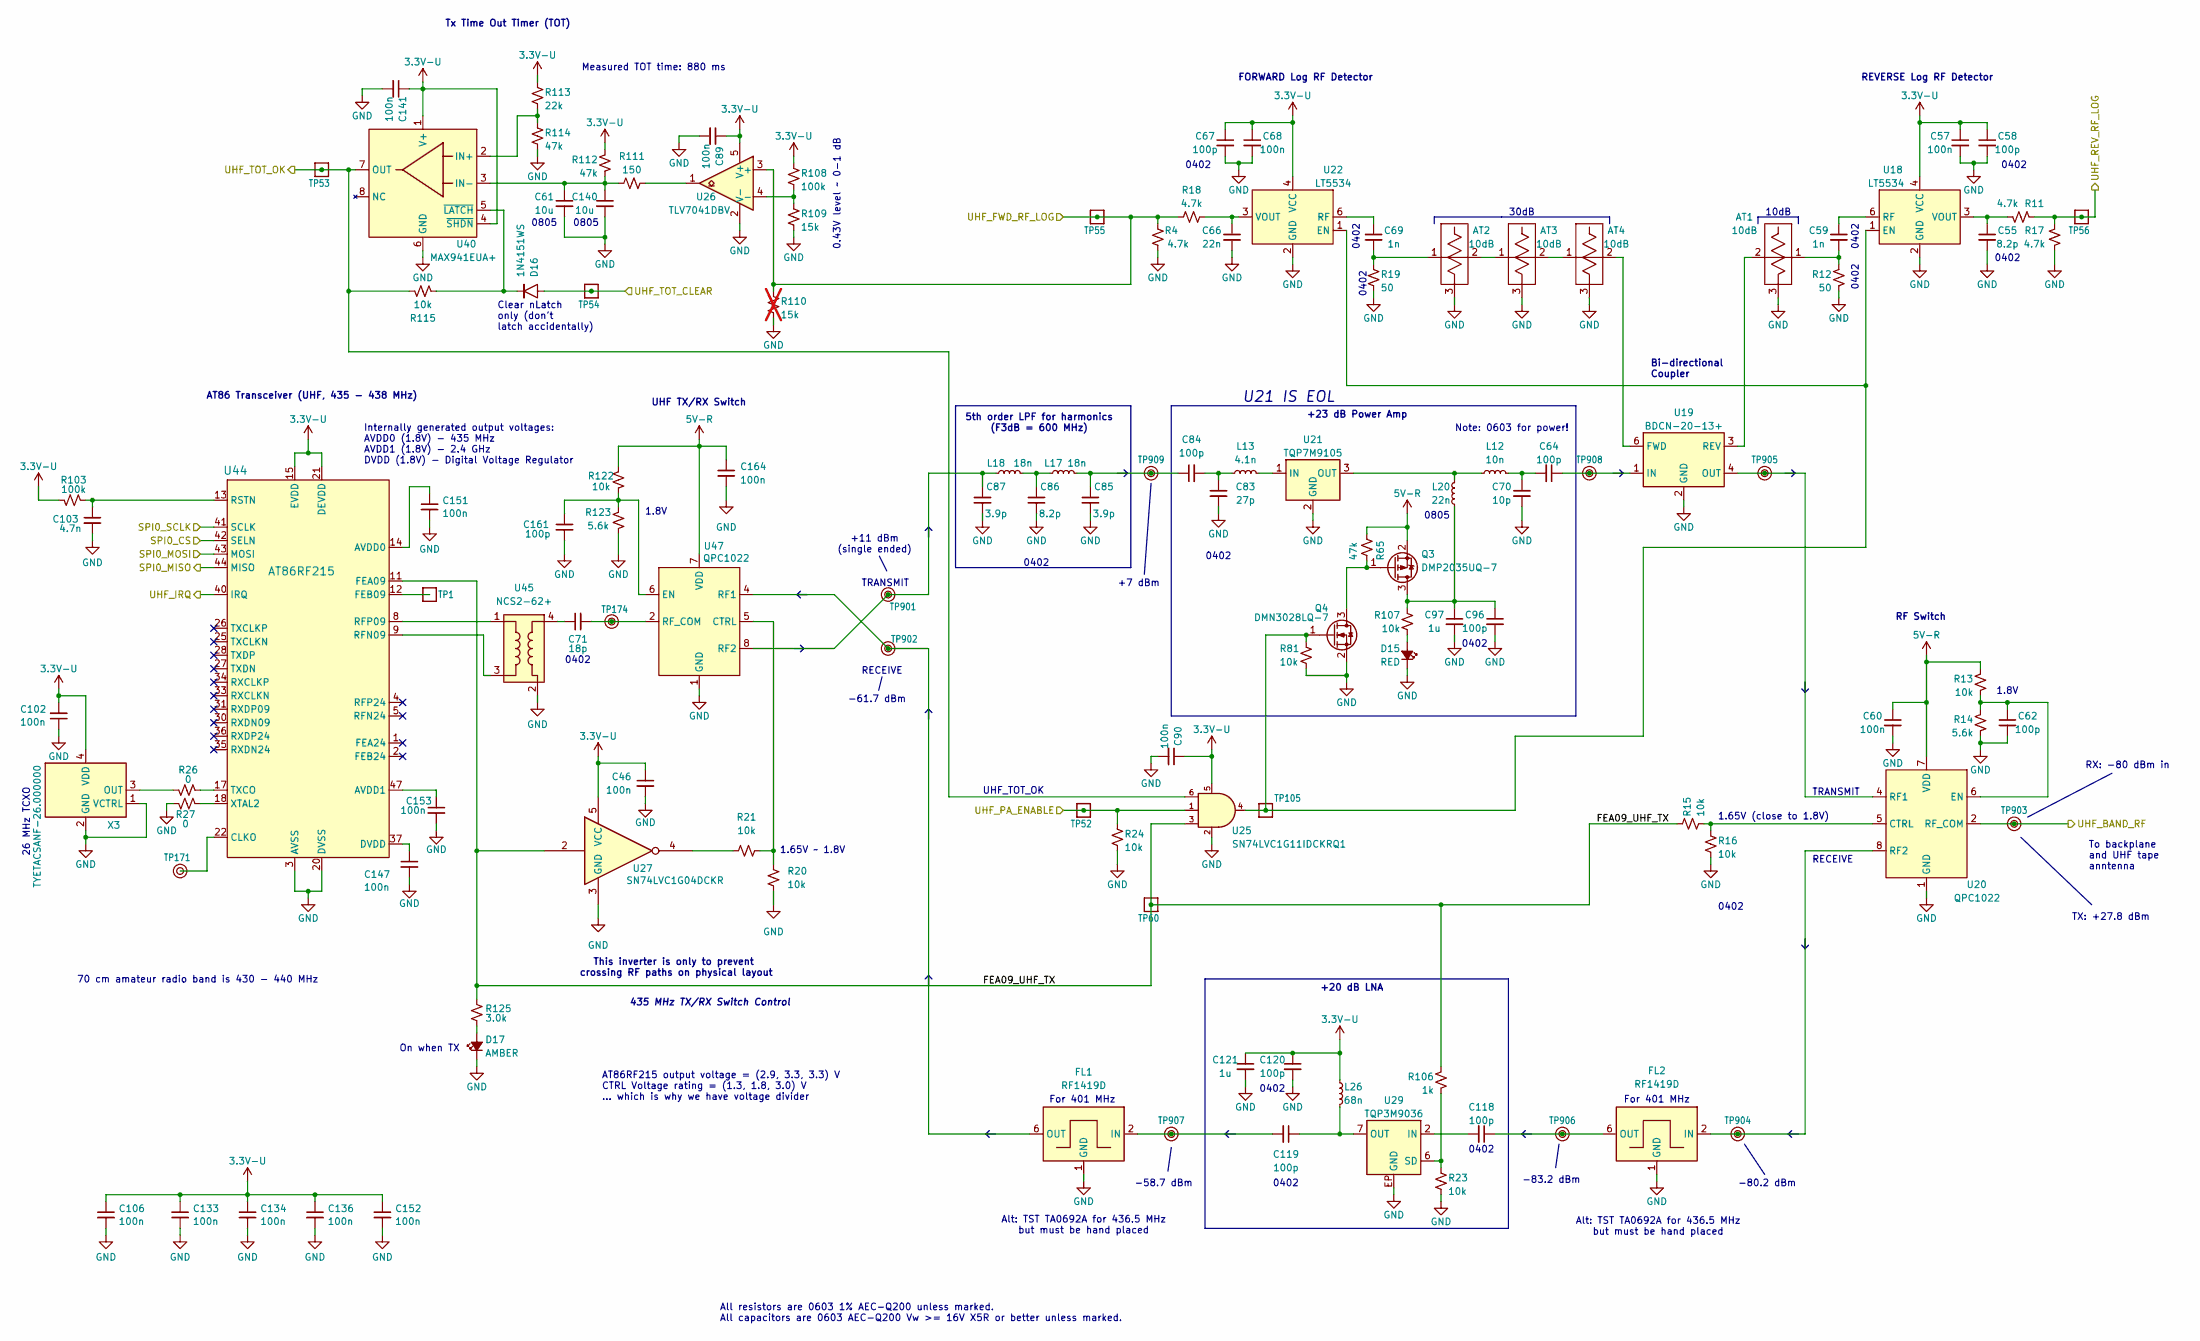
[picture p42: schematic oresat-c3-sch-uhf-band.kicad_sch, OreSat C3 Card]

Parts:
AT1, AT2, AT3, AT4: 10dB; PAT0816(0603); MPN PAT0816-C-10DB-T5
C46, C57, C60, C68, C89, C90, C102, C106, C133, C134, C136, C141, C147, C151, C152, C153, C164: 100n; 0603-C-NOSILK; MPN C0603C104K5RACAUTO
C55, C86: 8.2p; 0402-B-NOSILK; MPN GCQ1555C1H8R2BB01D
C58, C67, C84, C96, C118, C119, C120: 100p; 0402-B-NOSILK; MPN C0402C101J5GACAUTO
C59, C69: 1n; 0402-B-NOSILK; MPN C0402C102J3GACAUTO
C61, C140: 10u; 0805-C-NOSILK; MPN GRT21BC71E106KE13K
C62, C64, C161: 100p; 0603-C-NOSILK; MPN C0603C101K5HACAUTO
C66: 22n; 0603-C-NOSILK; MPN C0603C223K1RACAUTO
C70: 10p; 0603-C-NOSILK; MPN C0603C100J1GACAUTO
C71: 18p; 0402-B-NOSILK; MPN CBR04C180J5GACAUTO
C83: 27p; 0402-B-NOSILK; MPN C0402C270J5GACAUTO
C85, C87: 3.9p; 0402-B-NOSILK; MPN GCQ1555C1H3R9WB01D
C97, C121: 1u; 0603-C-NOSILK; MPN GRT188R71E105KE13D
C103: 4.7n; 0603-C-NOSILK; MPN C0603C472K5RACAUTO
D15: RED; LED_0603_1608Metric; MPN 150060RS75000
D16: 1N4151WS; D_SOD-323; MPN 1N4151WS-E3-08
D17: AMBER; LED_0603_1608Metric; MPN 150060AS75000
FL1, FL2: RF1419D; Filter_SAW-8_3.8x3.8mm; MPN RF1419D
L12: 10n; L_0603_1608Metric; MPN LQW18AN10NG00D
L13: 4.1n; L_0402_1005Metric; MPN LQW15AN4N1B00D
L17, L18: 18n; L_0402_1005Metric; MPN 0402HP-18NXGL
L20: 22n; L_0805_2012Metric; MPN LQW2BAN22NG00L
L26: 68n; L_0603_1608Metric; MPN LQW18AN68NG8ZD
Q3: DMP2035UQ-7; SOT-23; MPN DMP2035UQ-7
Q4: DMN3028LQ-7; SOT-23-3; MPN DMN3028LQ-7
R4, R11, R17, R18: 4.7k; 0603-C-NOSILK; MPN RMCF0603FT4K70
R12, R19: 50; 0402-B-NOSILK; MPN CH0402-50RJNPA
R13, R15, R16, R20, R21, R23, R24, R81, R107, R115, R122: 10k; 0603-C-NOSILK; MPN RMCF0603FT10K0
R14, R123: 5.6k; 0603-C-NOSILK; MPN RMCF0603FT5K60
R26, R27: 0; 0603-C-NOSILK; MPN RMCF0603ZT0R00
R65, R112, R114: 47k; 0603-C-NOSILK; MPN RMCF0603FT47K0
R103, R108: 100k; 0603-C-NOSILK; MPN RMCF0603FT100K
R106: 1k; 0603-C-NOSILK; MPN RMCF0603FT1K00
R109: 15k; 0603-C-NOSILK; MPN RMCF0603FT15K0
R110: 15k; R_0603_1608Metric; not fitted
R111: 150; 0603-C-NOSILK; MPN RMCF0603FT150R
R113: 22k; 0603-C-NOSILK; MPN RMCF0603FT22K0
R125: 3.0k; 0603-C-NOSILK; MPN RMCF0603FT3K00
TP1, TP52, TP53, TP54, TP55, TP56, TP60, TP105: Test-Point; TestPoint_Pad_D1.0mm
TP171, TP174, TP901, TP902, TP903, TP904, TP905, TP906, TP907, TP908, TP909: TestPoint_RF_Probe
U18, U22: LT5534; SOT-363_SC-70-6; MPN LT5534ESC6#TRPBF
U19: BDCN-20-13+; MPN BDCN-20-13+
U20, U47: QPC1022; MPN QPC1022TR7
U21: TQP7M9105; U-QORVO-TQP7M9105-VIAS; MPN TQP7M9105
U25: SN74LVC1G11IDCKRQ1; Texas_R-PDSO-G6; MPN SN74LVC1G11IDCKRQ1
U26: TLV7041DBV; SOT-23-5; MPN TLV7041DBVR
U27: SN74LVC1G04DCKR; SOT-353_SC-70-5; MPN SN74LVC1G04QDCKRQ1
U29: TQP3M9036; U-Qorvo-TQP3M9036-QFN-8-MO-220E; MPN TQP3M9036
U40: MAX941EUA+; LINEAR-MSOP-8-AND-MAXIM-UMAX-8-21-0036; MPN MAX941EUA+
U44: AT86RF215; QFN-48-1EP_7x7mm_P0.5mm_EP5.6x5.6mm; MPN AT86RF215-ZUR
U45: NCS2-62+; 2450FB15A050E_JOT; MPN NCS2-62+
X3: TYETACSANF-26.000000; X_TCXO_SMD_Taitien_2.5x2.0mm; MPN TYETACSANF-26.000000

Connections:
3.3V-U: C46.1, C57.1, C58.1, C67.1, C68.1, C89.1, C90.1, C102.2, C106.1, C120.1, C121.1, C133.1, C134.1, C136.1, C141.1, C152.1, L26.1, R103.2, R108.1, R112.1, R113.1, U18.4 (VCC), U22.4 (VCC), U25.5, U26.5 (V+), U27.5 (VCC), U40.1 (V+), U40.4 (~SHDN), U44.15 (EVDD), U44.21 (DEVDD), U44.29 (DEVDD), U44.39 (DEVDD), U44.46 (EVDD), X3.4 (VDD); also elsewhere on the board
5V-R: C60.1, C164.1, Q3.2 (S), R13.1, R65.1, R122.1, U20.7 (VDD), U47.7 (VDD); also elsewhere on the board
/OSD3358: SIP B/UHF_FWD_RF_LOG: R4.1, R18.1, R110.1, TP55.1 (1_1), U26.3 (+); also elsewhere on the board
/OSD3358: SIP B/UHF_REV_RF_LOG: R11.1, R17.1, TP56.1 (1_1); also elsewhere on the board
/OSD3358: SIP C/SPI0_CS: U44.42 (SELN); also elsewhere on the board
/OSD3358: SIP C/SPI0_MISO: U44.44 (MISO); also elsewhere on the board
/OSD3358: SIP C/SPI0_MOSI: U44.43 (MOSI); also elsewhere on the board
/OSD3358: SIP C/SPI0_SCLK: U44.41 (SCLK); also elsewhere on the board
/OSD3358: SIP C/UHF_IRQ: U44.40 (IRQ); also elsewhere on the board
/OSD3358: SIP C/UHF_PA_ENABLE: R24.1, TP52.1 (1_1), U25.1; also elsewhere on the board
/OSD3358: SIP C/UHF_TOT_CLEAR: D16.2, TP54.1 (1_1); also elsewhere on the board
/OSD3358: SIP C/UHF_TOT_OK: R115.1, TP53.1 (1_1), U25.6, U40.7 (OUT); also elsewhere on the board
/UHF Band/FEA09_UHF_TX: R15.1, R106.1, R125.1, TP60.1 (1_1), U25.3, U27.2, U44.11 (FEA09)
/UHF_BAND_RF: TP903.1 (1_1), U20.2 (RF_COM); also elsewhere on the board
GND: AT1.3, AT2.3, AT3.3, AT4.3, C46.2, C55.2, C57.2, C58.2, C60.2, C61.2, C62.2, C66.2, C67.2, C68.2, C70.2, C83.2, C85.2, C86.2, C87.2, C89.2, C90.2, C96.2, C97.2, C102.1, C103.2, C106.2, C120.2, C121.2, C133.2, C134.2, C136.2, C140.2, C141.2, C147.2, C151.2, C152.2, C153.2, C161.2, C164.2, D15.1 (K), D17.1 (K), FL1.1 (GND), FL1.3 (GND), FL1.4 (GND), FL1.5 (GND), FL1.7 (GND), FL1.8 (GND), FL2.1 (GND), FL2.3 (GND), FL2.4 (GND), FL2.5 (GND), FL2.7 (GND), FL2.8 (GND), Q4.2 (S), R4.2, R12.2, R14.2, R16.2, R17.2, R19.2, R20.1, R23.2, R24.2, R27.2, R81.2, R109.2, R110.2, R114.2, R123.2, U18.2 (GND), U18.5 (GND), U19.2 (GND), U19.5 (GND), U20.1 (GND), U20.3 (GND), U20.9 (GND), U21.2 (GND), U21.EP (GND), U22.2 (GND), U22.5 (GND), U25.2, U26.2 (V-), U27.3 (GND), U29.EP (GND), U40.6 (GND), U44.3 (AVSS), U44.6 (AVSS), U44.7 (AVSS), U44.10 (AVSS), U44.16 (AVSS), U44.19 (AVSS), U44.20 (DVSS), U44.23 (DVSS), U44.24 (DVSS), U44.32 (DVSS), U44.38 (DVSS), U44.45 (AVSS), U44.48 (AVSS), U44.49 (AVSS), U45.2 (GND), U45.6 (GND), U47.1 (GND), U47.3 (GND), U47.9 (GND), X3.1 (VCTRL), X3.2 (GND); also elsewhere on the board
unnamed: AT1.1, C59.2, R12.1
unnamed: AT2.1, C69.2, R19.1
unnamed: AT2.2, AT3.1
unnamed: AT3.2, AT4.1
unnamed: C64.2, C70.1, L12.1
unnamed: C71.1, U45.4
unnamed: C83.1, C84.2, L13.2
unnamed: C84.1, C85.1, L17.1, TP909.1 (1_1)
unnamed: C86.1, L17.2, L18.1
unnamed: D15.2 (A), R107.1
unnamed: D17.2 (A), R125.2
unnamed: C119.2, FL1.2 (IN), TP907.1 (1_1)
unnamed: FL1.6 (OUT), TP902.1 (1_1), U47.4 (RF1)
unnamed: FL2.2 (IN), TP904.1 (1_1), U20.8 (RF2)
unnamed: C118.1, FL2.6 (OUT), TP906.1 (1_1)
unnamed: C96.1, C97.1, L20.2, Q3.3 (D), R107.2
unnamed: Q3.1 (G), Q4.3 (D), R65.2
unnamed: Q4.1 (G), R81.1, TP105.1 (1_1), U18.1 (EN), U22.1 (EN), U25.4
unnamed: R21.2, U27.4
unnamed: R111.2, U26.1
unnamed: C59.1, U18.6 (RF)
unnamed: C55.1, R11.2, U18.3 (VOUT)
unnamed: AT4.2, U19.6 (FWD)
unnamed: C64.1, TP908.1 (1_1), U19.1 (IN)
unnamed: TP905.1 (1_1), U19.4 (OUT), U20.4 (RF1)
unnamed: AT1.2, U19.3 (REV)
unnamed: R15.2, R16.1, U20.5 (CTRL)
unnamed: C62.1, R13.2, R14.1, U20.6 (EN)
unnamed: L13.1, U21.1 (IN)
unnamed: L12.2, L20.1, U21.3 (OUT)
unnamed: C69.1, U22.6 (RF)
unnamed: C66.1, R18.2, U22.3 (VOUT)
unnamed: R108.2, R109.1, U26.4 (-)
unnamed: C118.2, U29.2 (IN)
unnamed: C119.1, L26.2, U29.7 (OUT)
unnamed: R23.1, R106.2, U29.6 (SD)
unnamed: R113.2, R114.1, U40.2 (IN+)
unnamed: C61.1, C140.1, R111.1, R112.2, U40.3 (IN-)
unnamed: D16.1, R115.2, U40.5 (~LATCH)
unnamed: C151.1, U44.14 (AVDD0)
unnamed: C153.1, U44.47 (AVDD1)
unnamed: TP171.1 (1_1), U44.22 (CLKO)
unnamed: C147.1, U44.37 (DVDD)
unnamed: TP1.1 (1_1), U44.12 (FEB09)
unnamed: U44.9 (RFN09), U45.3
unnamed: U44.8 (RFP09), U45.1
unnamed: C103.1, R103.1, U44.13 (RSTN)
unnamed: R26.1, U44.17 (TXCO)
unnamed: R27.1, U44.18 (XTAL2)
unnamed: R20.2, R21.1, U47.5 (CTRL)
unnamed: C161.1, R122.2, R123.1, U47.6 (EN)
unnamed: C87.1, L18.2, TP901.1 (1_1), U47.8 (RF2)
unnamed: C71.2, TP174.1 (1_1), U47.2 (RF_COM)
unnamed: R26.2, X3.3 (OUT)

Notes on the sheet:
AT86 Transceiver (UHF, 435 - 438 MHz)
To backplane and UHF tape anntenna
-80.2 dBm
0402
Alt: TST TA0692A for 436.5 MHz but must be hand placed
-83.2 dBm
+20 dB LNA
Clear nLatch only (don't latch accidentally)
+7 dBm
RECEIVE
RX: -80 dBm in
Tx Time Out Timer (TOT)
AT86RF215 output voltage = (2.9, 3.3, 3.3) V CTRL Voltage rating = (1.3, 1.8, 3.0) V ... which is why we have voltage divider
REVERSE Log RF Detector
For 401 MHz
TRANSMIT
5th order LPF for harmonics (F3dB = 600 MHz)
10dB
0805
-58.7 dBm
26 MHz TCXO
1.65V (close to 1.8V)
U21 IS EOL
Internally generated output voltages: AVDD0 (1.8V) - 435 MHz AVDD1 (1.8V) - 2.4 GHz DVDD (1.8V) - Digital Voltage Regulator
Note: 0603 for power!
Measured TOT time: 880 ms
On when TX
-61.7 dBm
+23 dB Power Amp
30dB
1.8V
1.65V ~ 1.8V
+11 dBm (single ended)
This inverter is only to prevent crossing RF paths on physical layout
UHF_TOT_OK
435 MHz TX/RX Switch Control
70 cm amateur radio band is 430 - 440 MHz
Bi-directional Coupler
RF Switch
0.43V level ~ 0-1 dB

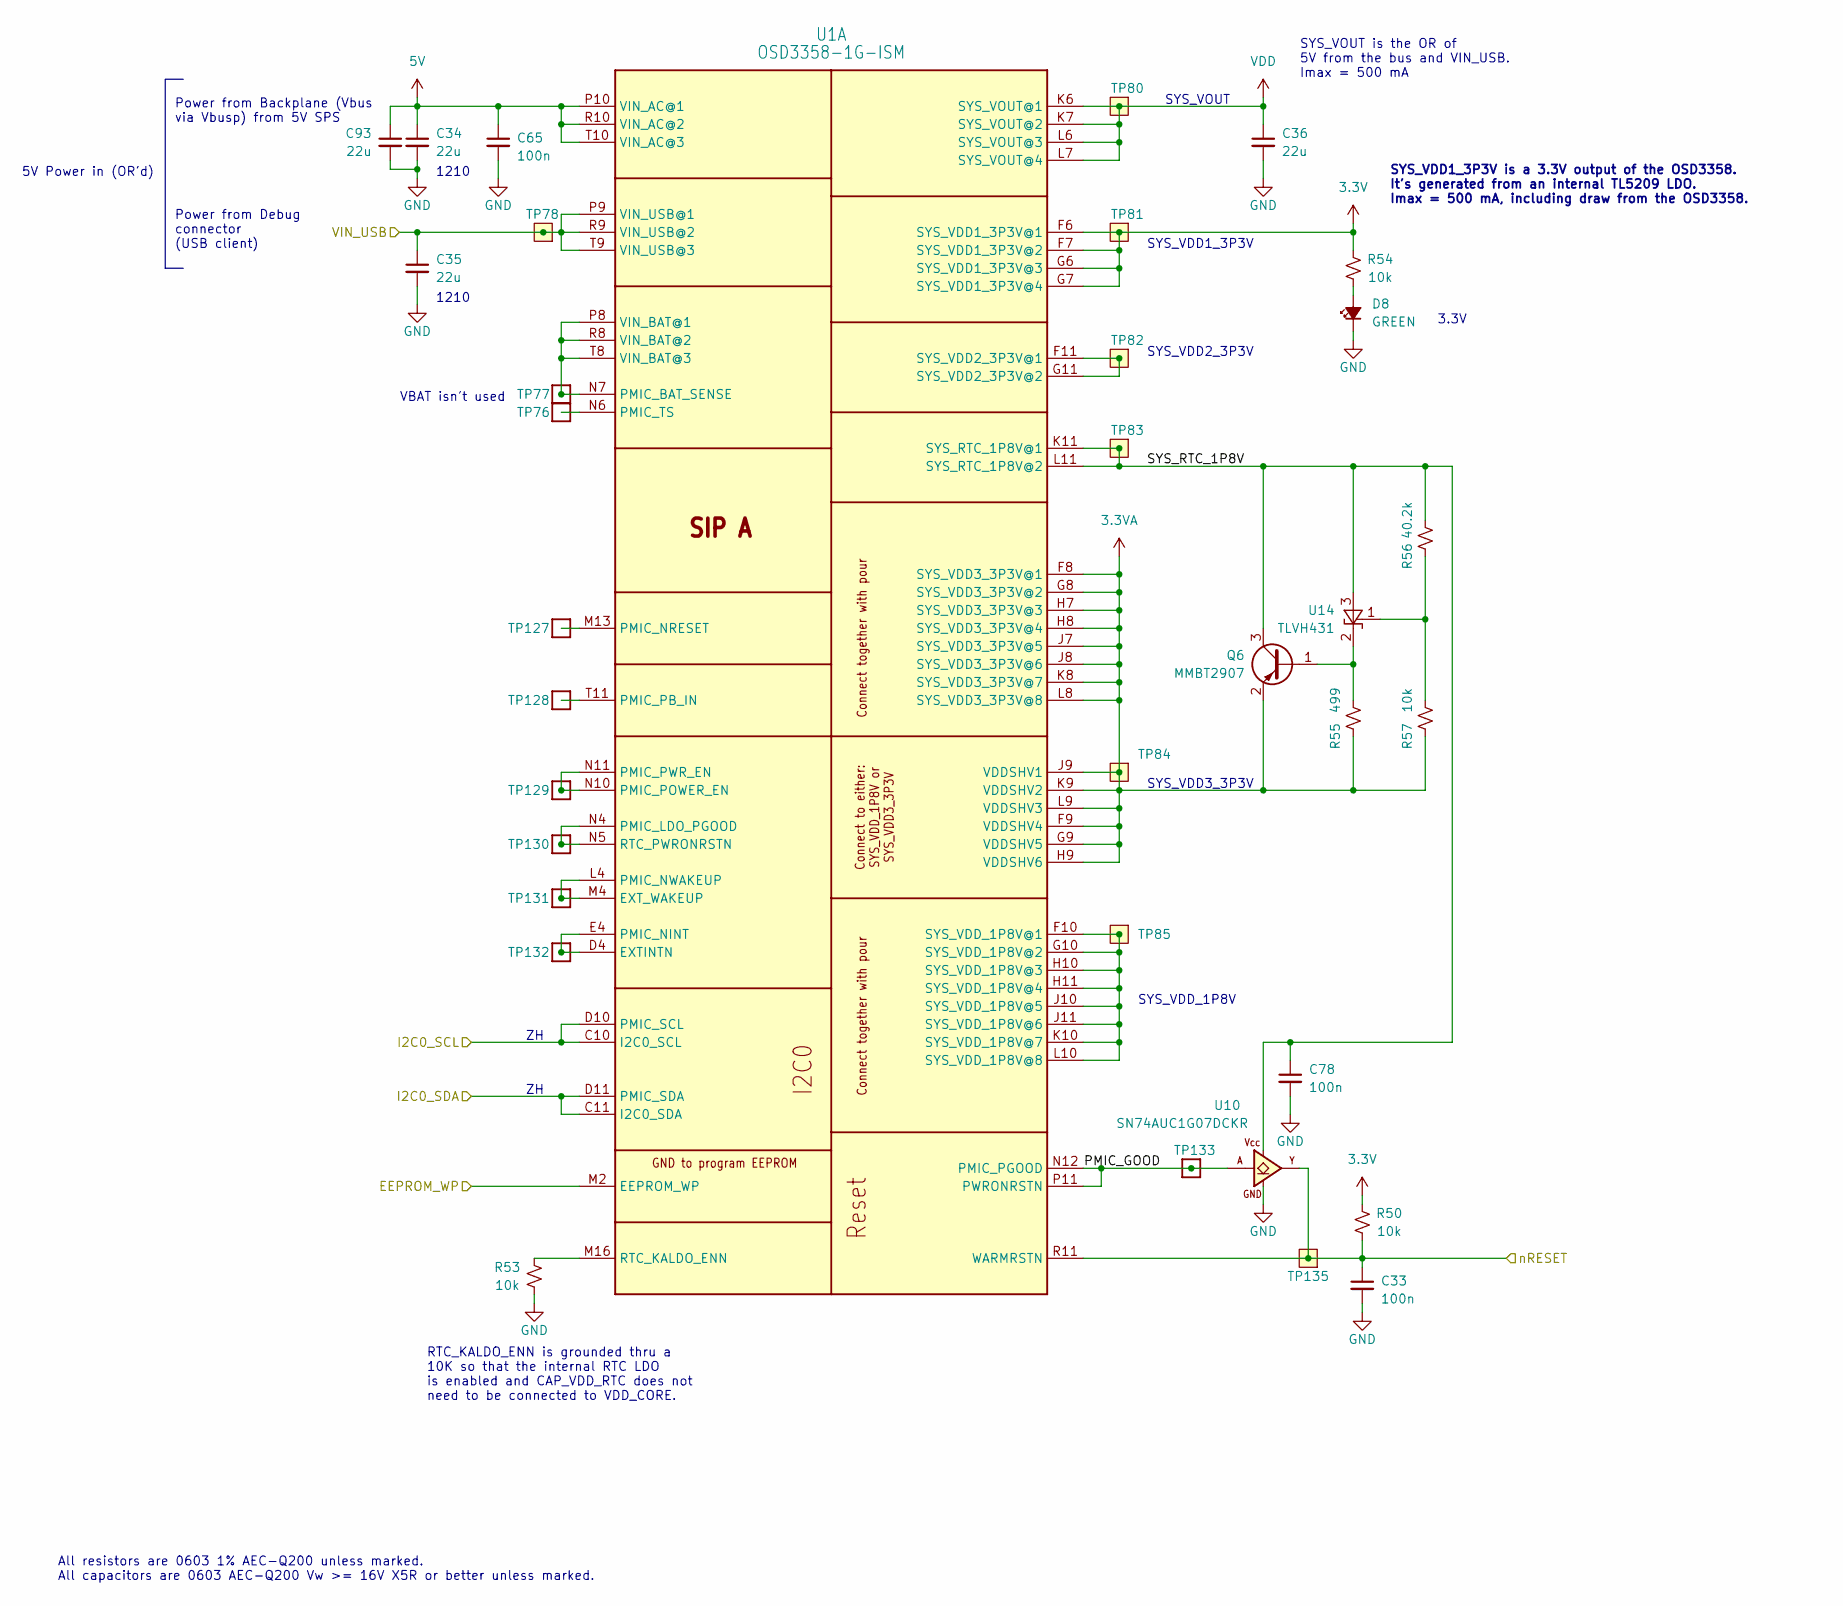
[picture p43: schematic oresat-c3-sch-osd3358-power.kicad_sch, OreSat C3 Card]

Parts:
C33, C65, C78: 100n; 0603-C-NOSILK; MPN C0603C104K5RACAUTO
C34, C35, C36, C93: 22u; C_1210_3225Metric; MPN TMK325B7226KMHP
D8: GREEN; LED_0603_1608Metric; MPN 150060GS75000
Q6: MMBT2907; SOT-23; MPN PMBT2907A,215
R50, R53, R54, R57: 10k; 0603-C-NOSILK; MPN RMCF0603FT10K0
R55: 499; 0603-C-NOSILK; MPN RMCF0603FT499R
R56: 40.2k; 0603-C-NOSILK; MPN RMCF0603FT40K2
TP76, TP77, TP127, TP128, TP129, TP130, TP131, TP132, TP133: Test-Point; TestPoint_Pad_D1.0mm
TP78, TP80, TP81, TP82, TP83, TP84, TP85, TP135: Test-Point; TestPoint-0.75mm-th
U1: OSD3358-1G-ISM; U-Octavo-OSD335X-BGA-256; MPN OSD3358-512M-BSM
U10: SN74AUC1G07DCKR; SOT-353_SC-70-5; MPN SN74AUC1G07DCKR
U14: TLVH431; SOT-23; MPN TLVH431BCDBZT

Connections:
3.3V: R50.2, R54.1, TP81.1 (1_1), U1.F6 (SYS_VDD1_3P3V@1), U1.F7 (SYS_VDD1_3P3V@2), U1.G6 (SYS_VDD1_3P3V@3), U1.G7 (SYS_VDD1_3P3V@4); also elsewhere on the board
3.3VA: Q6.2 (E), R55.1, R57.1, TP84.1 (1_1), U1.F8 (SYS_VDD3_3P3V@1), U1.F9 (VDDSHV4), U1.G8 (SYS_VDD3_3P3V@2), U1.G9 (VDDSHV5), U1.H7 (SYS_VDD3_3P3V@3), U1.H8 (SYS_VDD3_3P3V@4), U1.H9 (VDDSHV6), U1.J7 (SYS_VDD3_3P3V@5), U1.J8 (SYS_VDD3_3P3V@6), U1.J9 (VDDSHV1), U1.K8 (SYS_VDD3_3P3V@7), U1.K9 (VDDSHV2), U1.L8 (SYS_VDD3_3P3V@8), U1.L9 (VDDSHV3)
5V: C34.1, C65.1, C93.1, U1.P10 (VIN_AC@1), U1.R10 (VIN_AC@2), U1.T10 (VIN_AC@3); also elsewhere on the board
/OSD3358: SIP A/EEPROM_WP: U1.M2 (EEPROM_WP); also elsewhere on the board
/OSD3358: SIP A/I2C0_SCL: U1.C10 (I2C0_SCL), U1.D10 (PMIC_SCL); also elsewhere on the board
/OSD3358: SIP A/I2C0_SDA: U1.C11 (I2C0_SDA), U1.D11 (PMIC_SDA); also elsewhere on the board
/OSD3358: SIP A/PMIC_GOOD: TP133.1 (1_1), U1.N12 (PMIC_PGOOD), U1.P11 (PWRONRSTN), U10.2 (A)
/OSD3358: SIP A/SYS_RTC_1P8V: C78.1, Q6.3 (C), R56.2, TP83.1 (1_1), U1.K11 (SYS_RTC_1P8V@1), U1.L11 (SYS_RTC_1P8V@2), U10.5 (VCC), U14.3 (A)
/OSD3358: SIP A/nRESET: C33.1, R50.1, TP135.1 (1_1), U1.R11 (WARMRSTN), U10.4 (Y); also elsewhere on the board
/VIN_USB: C35.1, TP78.1 (1_1), U1.P9 (VIN_USB@1), U1.R9 (VIN_USB@2), U1.T9 (VIN_USB@3); also elsewhere on the board
GND: C33.2, C34.2, C35.2, C36.2, C65.2, C78.2, C93.2, D8.1 (K), R53.1, U10.3 (GND); also elsewhere on the board
unnamed: D8.2 (A), R54.2
unnamed: Q6.1 (B), R55.2, U14.2 (K)
unnamed: TP132.1 (1_1), U1.D4 (EXTINTN), U1.E4 (PMIC_NINT)
unnamed: TP131.1 (1_1), U1.L4 (PMIC_NWAKEUP), U1.M4 (EXT_WAKEUP)
unnamed: TP77.1 (1_1), U1.N7 (PMIC_BAT_SENSE), U1.P8 (VIN_BAT@1), U1.R8 (VIN_BAT@2), U1.T8 (VIN_BAT@3)
unnamed: TP130.1 (1_1), U1.N4 (PMIC_LDO_PGOOD), U1.N5 (RTC_PWRONRSTN)
unnamed: TP127.1 (1_1), U1.M13 (PMIC_NRESET)
unnamed: TP128.1 (1_1), U1.T11 (PMIC_PB_IN)
unnamed: TP129.1 (1_1), U1.N10 (PMIC_POWER_EN), U1.N11 (PMIC_PWR_EN)
unnamed: TP76.1 (1_1), U1.N6 (PMIC_TS)
unnamed: R53.2, U1.M16 (RTC_KALDO_ENN)
unnamed: TP82.1 (1_1), U1.F11 (SYS_VDD2_3P3V@1), U1.G11 (SYS_VDD2_3P3V@2)
unnamed: TP85.1 (1_1), U1.F10 (SYS_VDD_1P8V@1), U1.G10 (SYS_VDD_1P8V@2), U1.H10 (SYS_VDD_1P8V@3), U1.H11 (SYS_VDD_1P8V@4), U1.J10 (SYS_VDD_1P8V@5), U1.J11 (SYS_VDD_1P8V@6), U1.K10 (SYS_VDD_1P8V@7), U1.L10 (SYS_VDD_1P8V@8)
unnamed: R56.1, R57.2, U14.1 (REF)
VDD: C36.1, TP80.1 (1_1), U1.K6 (SYS_VOUT@1), U1.K7 (SYS_VOUT@2), U1.L6 (SYS_VOUT@3), U1.L7 (SYS_VOUT@4)

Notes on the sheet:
1210
All resistors are 0603 1% AEC-Q200 unless marked. All capacitors are 0603 AEC-Q200 Vw >= 16V X5R or better unless marked.
SYS_VOUT
SYS_VDD_1P8V
Power from Backplane (Vbus via Vbusp) from 5V SPS
SYS_VDD3_3P3V
SYS_VDD1_3P3V is a 3.3V output of the OSD3358. It's generated from an internal TL5209 LDO. Imax = 500 mA, including draw from the OSD3358.
Power from Debug connector (USB client)
SYS_VDD2_3P3V
SYS_VDD1_3P3V
RTC_KALDO_ENN is grounded thru a 10K so that the internal RTC LDO is enabled and CAP_VDD_RTC does not need to be connected to VDD_CORE.
VBAT isn't used
SYS_VOUT is the OR of 5V from the bus and VIN_USB. Imax = 500 mA
5V Power in (OR'd)
3.3V

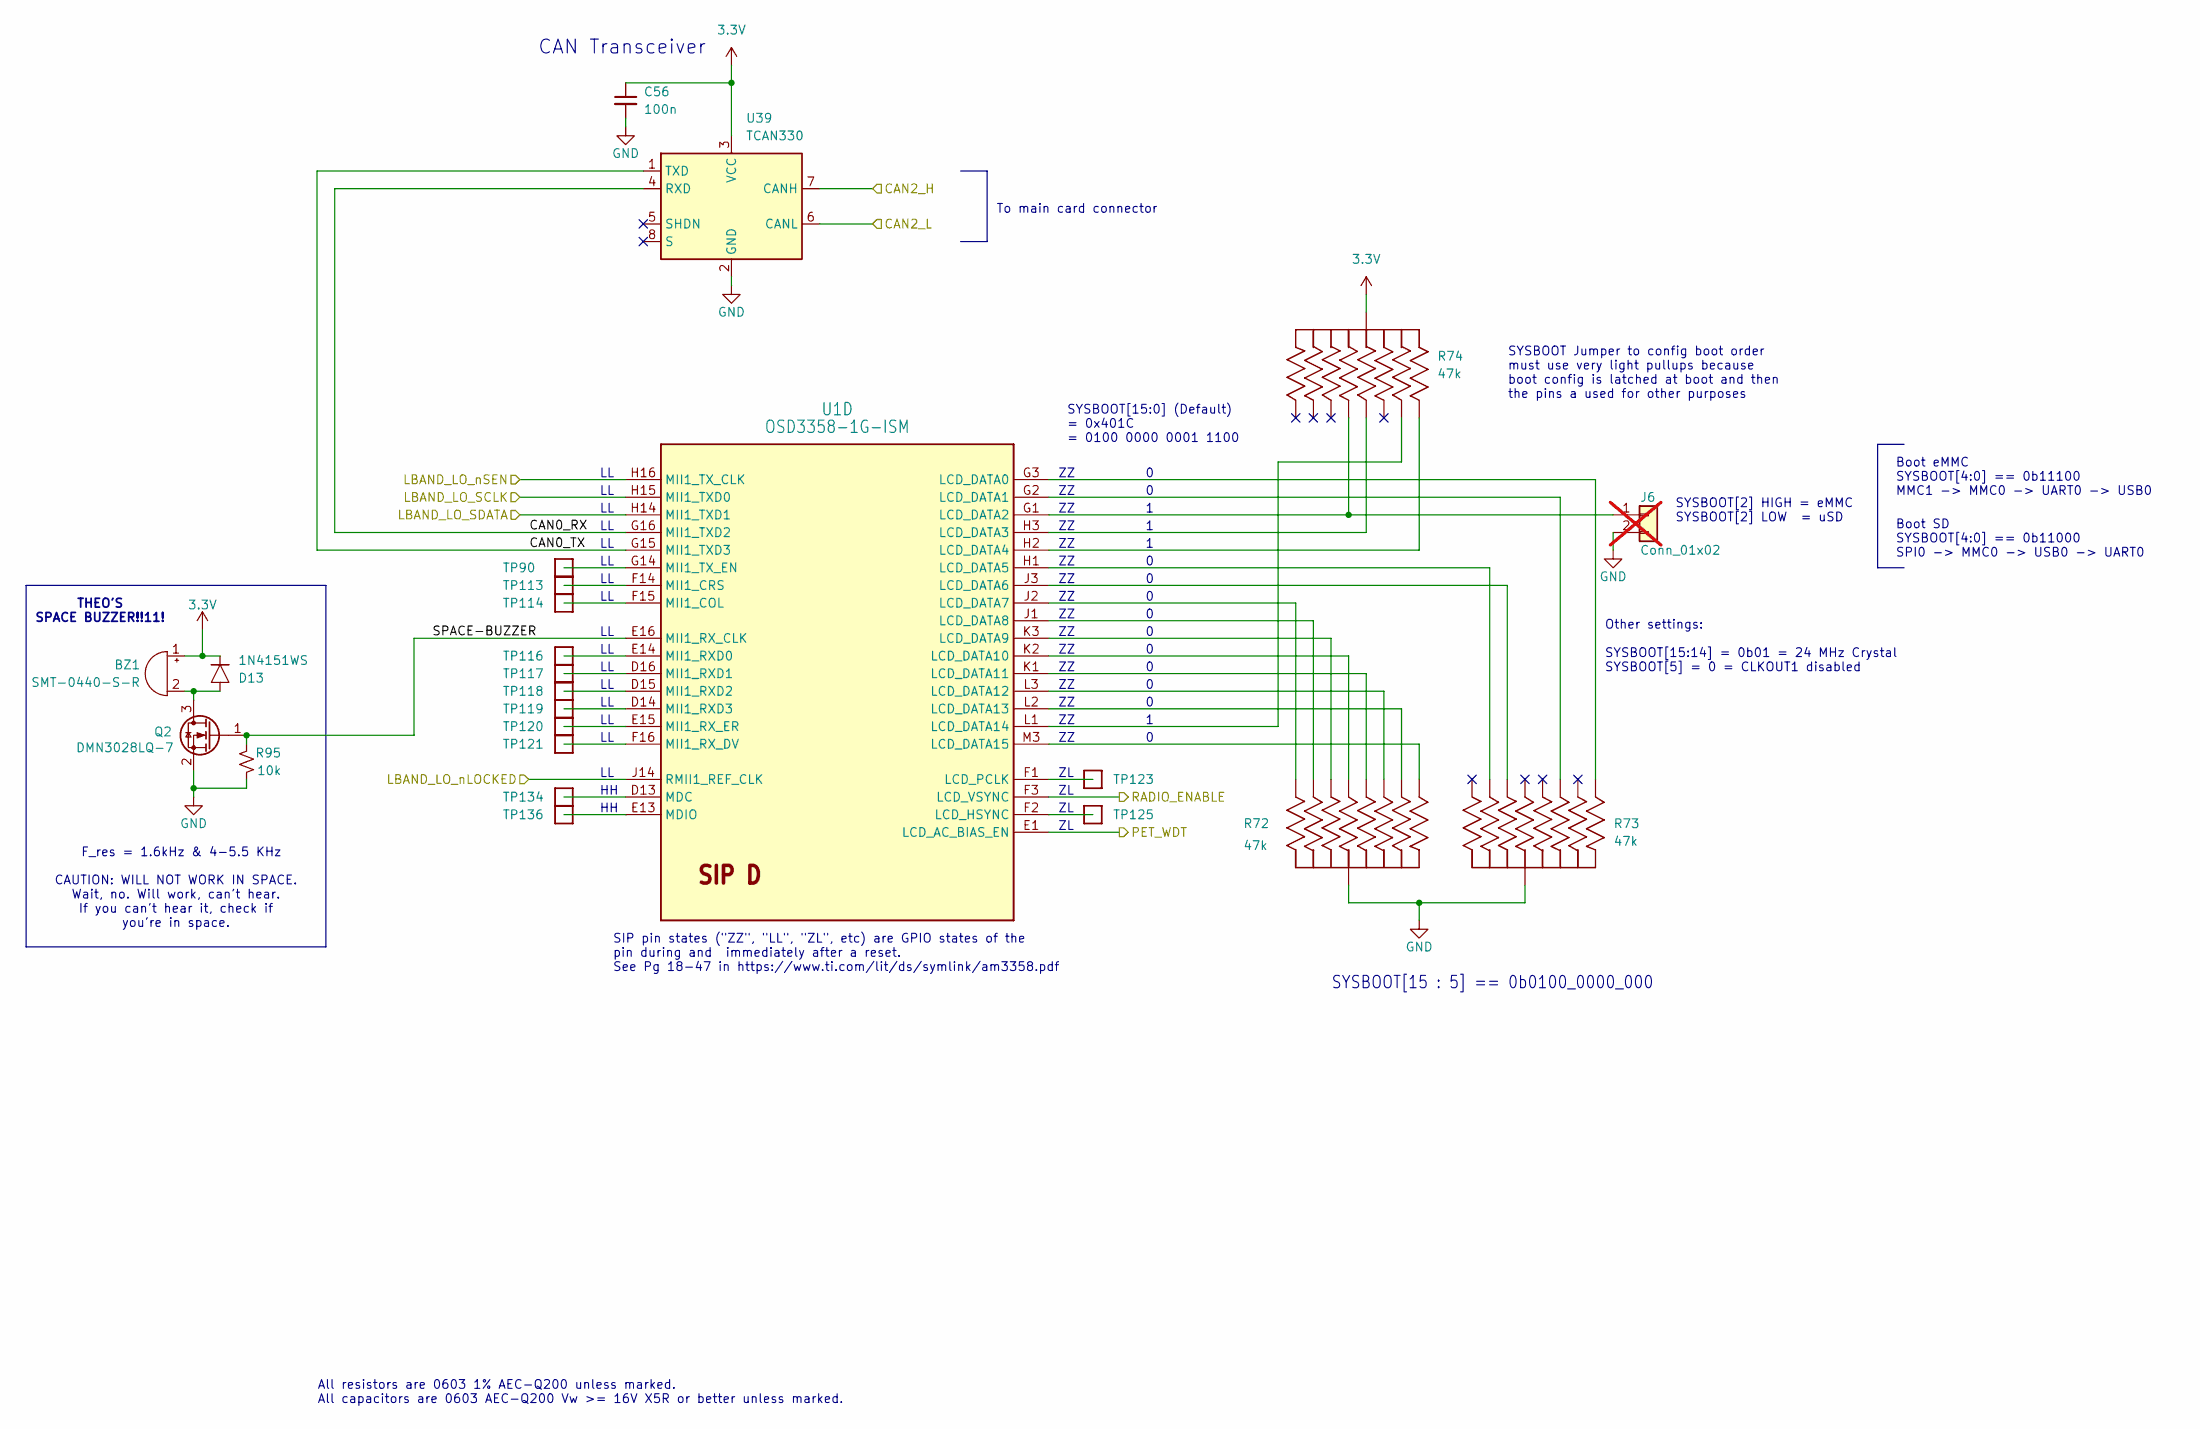
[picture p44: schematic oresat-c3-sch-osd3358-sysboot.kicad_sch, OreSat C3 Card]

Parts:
BZ1: SMT-0440-S-R; MPN SMT-0440-S-R
C56: 100n; 0603-C-NOSILK; MPN C0603C104K5RACAUTO
D13: 1N4151WS; D_SOD-323; MPN 1N4151WS-E3-08
J6: Conn_01x02; PinHeader_1x02_P2.54mm_Vertical; not fitted
Q2: DMN3028LQ-7; SOT-23-3; MPN DMN3028LQ-7
R72, R73, R74: 47k; Panasonic_Resistor_Array_EXBA10; MPN EXB-A10P473J
R95: 10k; 0603-C-NOSILK; MPN RMCF0603FT10K0
TP90, TP113, TP114, TP116, TP117, TP118, TP119, TP120, TP121, TP123, TP125, TP134, TP136: Test-Point; TestPoint_Pad_D1.0mm
U1: OSD3358-1G-ISM; U-Octavo-OSD335X-BGA-256; MPN OSD3358-512M-BSM
U39: TCAN330; SOT-23-8; MPN TCAN330GDCNT

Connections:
3.3V: BZ1.1 (+), C56.1, D13.1, R74.5 (55), R74.10 (55), U39.3 (VCC); also elsewhere on the board
/CAN2_H: U39.7 (CANH); also elsewhere on the board
/CAN2_L: U39.6 (CANL); also elsewhere on the board
/L Band/LBAND_LO_SCLK: U1.H15 (MII1_TXD0); also elsewhere on the board
/L Band/LBAND_LO_SDATA: U1.H14 (MII1_TXD1); also elsewhere on the board
/L Band/LBAND_LO_nLOCKED: U1.J14 (RMII1_REF_CLK); also elsewhere on the board
/L Band/LBAND_LO_nSEN: U1.H16 (MII1_TX_CLK); also elsewhere on the board
/OSD3358: SIP D/CAN0_RX: U1.G16 (MII1_TXD2), U39.4 (RXD)
/OSD3358: SIP D/CAN0_TX: U1.G15 (MII1_TXD3), U39.1 (TXD)
/OSD3358: SIP D/PET_WDT: U1.E1 (LCD_AC_BIAS_EN); also elsewhere on the board
/OSD3358: SIP D/RADIO_ENABLE: U1.F3 (LCD_VSYNC); also elsewhere on the board
/OSD3358: SIP D/SPACE-BUZZER: Q2.1 (G), R95.1, U1.E16 (MII1_RX_CLK)
GND: C56.2, J6.2, Q2.2 (S), R72.5 (55), R72.10 (55), R73.5 (55), R73.10 (55), R95.2, U39.2 (GND); also elsewhere on the board
unnamed: BZ1.2 (-), D13.2, Q2.3 (D)
unnamed: J6.1, R74.8 (88), U1.G1 (LCD_DATA2)
unnamed: R72.1 (11), U1.M3 (LCD_DATA15)
unnamed: R72.2 (22), U1.L3 (LCD_DATA12)
unnamed: R72.3 (33), U1.K2 (LCD_DATA10)
unnamed: R72.4 (44), U1.J1 (LCD_DATA8)
unnamed: R72.6 (66), U1.J2 (LCD_DATA7)
unnamed: R72.7 (77), U1.K3 (LCD_DATA9)
unnamed: R72.8 (88), U1.K1 (LCD_DATA11)
unnamed: R72.9 (99), U1.L2 (LCD_DATA13)
unnamed: R73.1 (11), U1.G3 (LCD_DATA0)
unnamed: R73.2 (22), U1.G2 (LCD_DATA1)
unnamed: R73.4 (44), U1.H1 (LCD_DATA5)
unnamed: R73.7 (77), U1.J3 (LCD_DATA6)
unnamed: R74.3 (33), U1.H3 (LCD_DATA3)
unnamed: R74.4 (44), U1.L1 (LCD_DATA14)
unnamed: R74.6 (66), U1.H2 (LCD_DATA4)
unnamed: TP125.1 (1_1), U1.F2 (LCD_HSYNC)
unnamed: TP123.1 (1_1), U1.F1 (LCD_PCLK)
unnamed: TP134.1 (1_1), U1.D13 (MDC)
unnamed: TP136.1 (1_1), U1.E13 (MDIO)
unnamed: TP114.1 (1_1), U1.F15 (MII1_COL)
unnamed: TP113.1 (1_1), U1.F14 (MII1_CRS)
unnamed: TP116.1 (1_1), U1.E14 (MII1_RXD0)
unnamed: TP117.1 (1_1), U1.D16 (MII1_RXD1)
unnamed: TP118.1 (1_1), U1.D15 (MII1_RXD2)
unnamed: TP119.1 (1_1), U1.D14 (MII1_RXD3)
unnamed: TP121.1 (1_1), U1.F16 (MII1_RX_DV)
unnamed: TP120.1 (1_1), U1.E15 (MII1_RX_ER)
unnamed: TP90.1 (1_1), U1.G14 (MII1_TX_EN)

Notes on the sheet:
THEO'S SPACE BUZZER!!11!
SYSBOOT[2] HIGH = eMMC SYSBOOT[2] LOW = uSD
SIP pin states ("ZZ", "LL", "ZL", etc) are GPIO states of the pin during and immediately after a reset. See Pg 18-47 in https://www.ti.com/lit/ds/symlink/am3358.pdf
Boot SD SYSBOOT[4:0] == 0b11000 SPI0 -> MMC0 -> USB0 -> UART0
All resistors are 0603 1% AEC-Q200 unless marked. All capacitors are 0603 AEC-Q200 Vw >= 16V X5R or better unless marked.
Boot eMMC SYSBOOT[4:0] == 0b11100 MMC1 -> MMC0 -> UART0 -> USB0
SYSBOOT[15:0] (Default) = 0x401C = 0100 0000 0001 1100
CAN Transceiver
SYSBOOT Jumper to config boot order must use very light pullups because boot config is latched at boot and then the pins a used for other purposes
F_res = 1.6kHz & 4-5.5 KHz
Other settings: SYSBOOT[15:14] = 0b01 = 24 MHz Crystal SYSBOOT[5] = 0 = CLKOUT1 disabled
SYSBOOT[15 : 5] == 0b0100_0000_000
To main card connector
CAUTION: WILL NOT WORK IN SPACE. Wait, no. Will work, can't hear. If you can't hear it, check if you're in space.

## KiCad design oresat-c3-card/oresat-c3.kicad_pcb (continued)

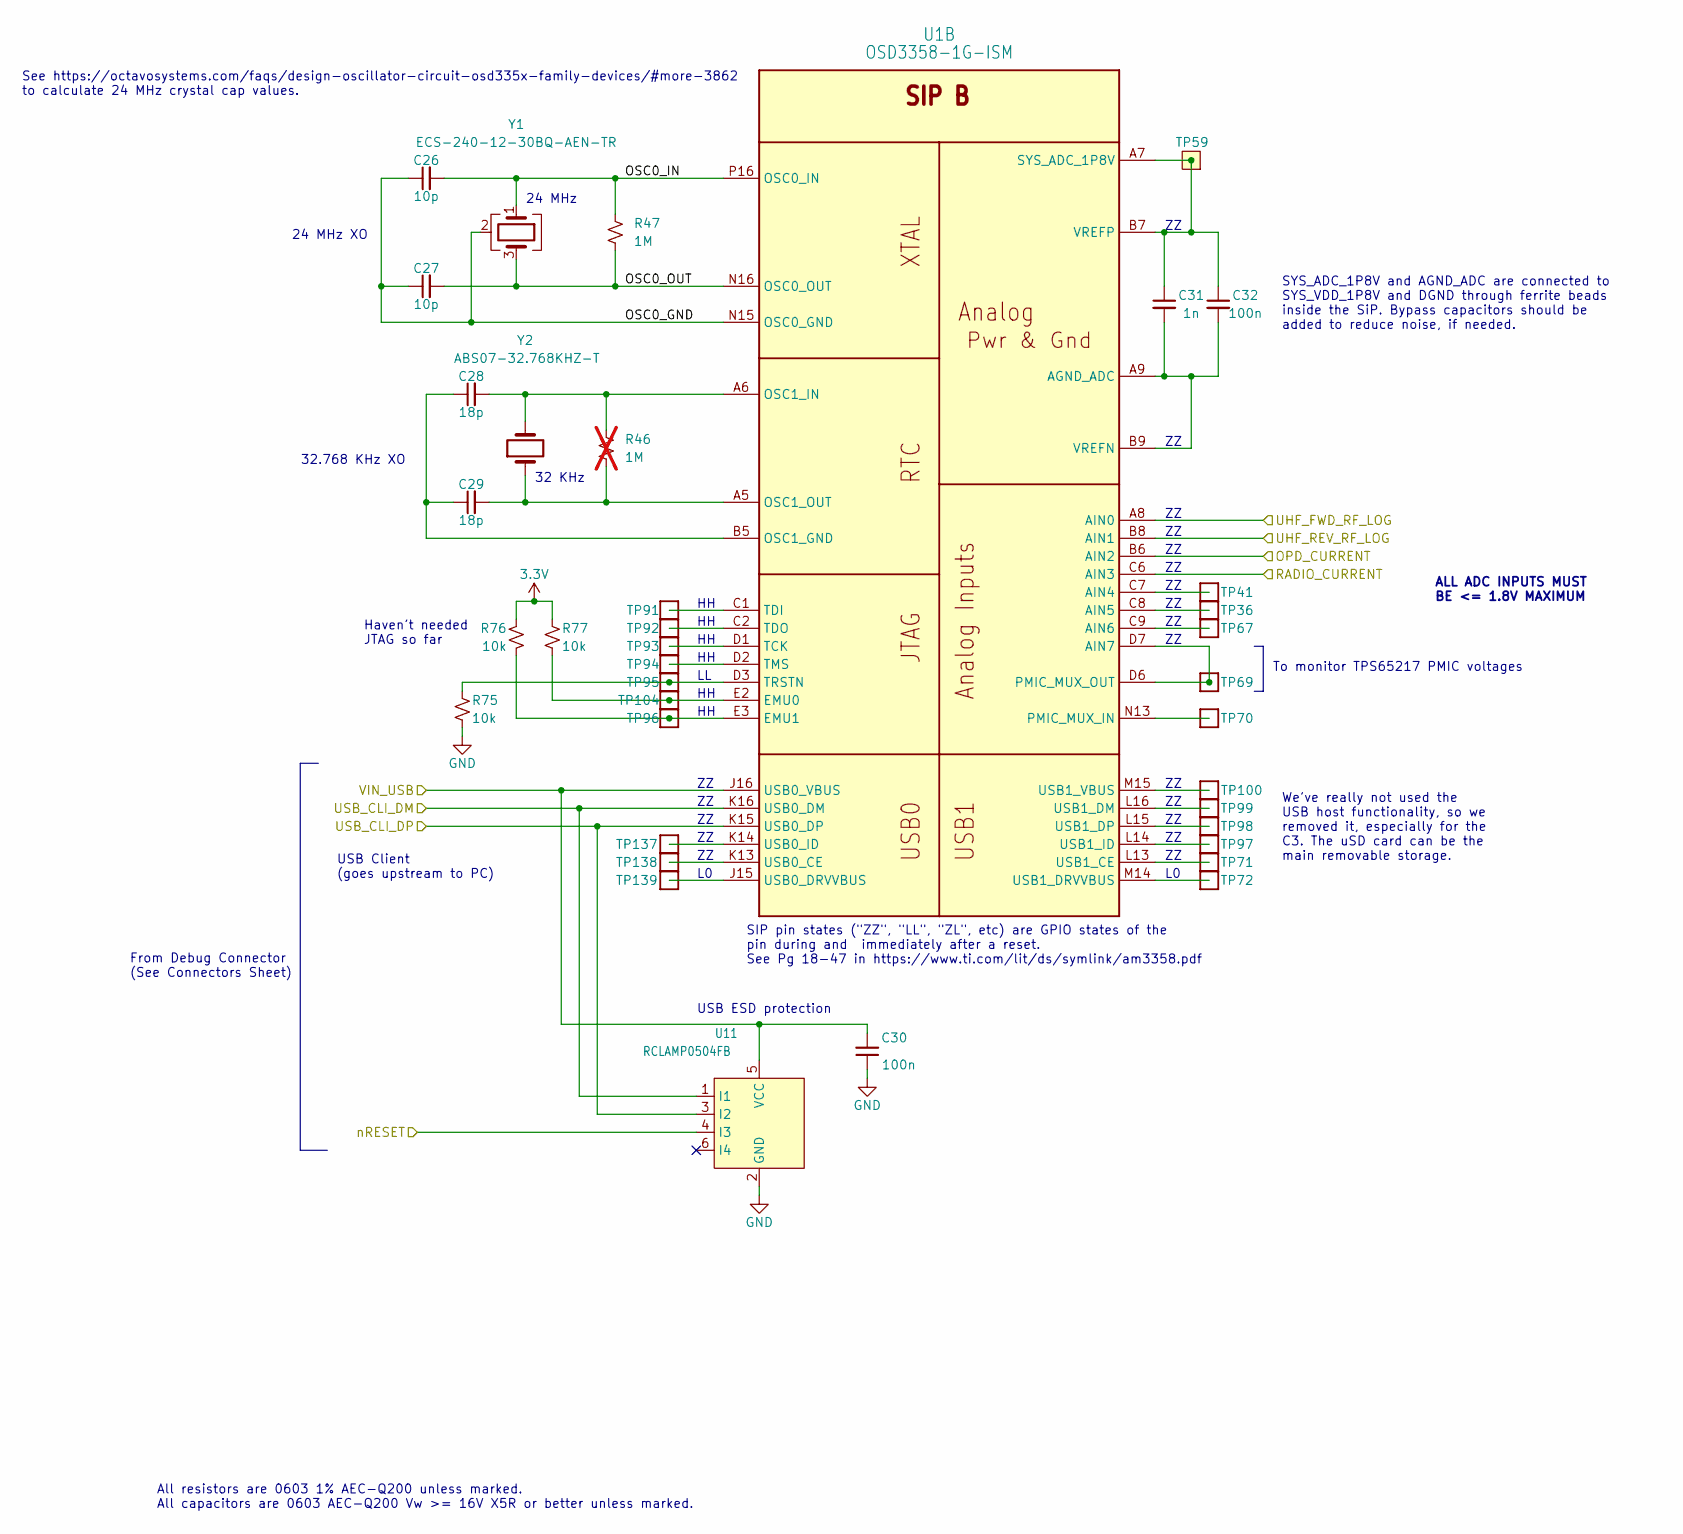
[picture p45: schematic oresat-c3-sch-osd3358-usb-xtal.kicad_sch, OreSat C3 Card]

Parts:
C26, C27: 10p; 0603-C-NOSILK; MPN C0603C100J1GACAUTO
C28, C29: 18p; 0603-C-NOSILK; MPN C0603C180F5GACAUTO
C30, C32: 100n; 0603-C-NOSILK; MPN C0603C104K5RACAUTO
C31: 1n; 0603-C-NOSILK; MPN C0603C102J5RACAUTO
R46: 1M; R_0603_1608Metric; not fitted
R47: 1M; 0603-C-NOSILK; MPN RMCF0603FG1M00
R75, R76, R77: 10k; 0603-C-NOSILK; MPN RMCF0603FT10K0
TP36, TP41, TP67, TP69, TP70, TP71, TP72, TP91, TP92, TP93, TP94, TP95, TP96, TP97, TP98, TP99, TP100, TP104, TP137, TP138, TP139: Test-Point; TestPoint_Pad_D1.0mm
TP59: Test-Point; TestPoint-0.75mm-th
U1: OSD3358-1G-ISM; U-Octavo-OSD335X-BGA-256; MPN OSD3358-512M-BSM
U11: RCLAMP0504FB; SOT-363_SC-70-6; MPN RCLAMP0504FBTCT
Y1: ECS-240-12-30BQ-AEN-TR; CRYSTAL-5X3.2-4SMD; MPN ECS-240-12-30BQ-AEN-TR
Y2: ABS07-32.768KHZ-T; CRYSTAL_3.2X1.5; MPN ABS07-32.768KHZ-T

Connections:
3.3V: R76.1, R77.1; also elsewhere on the board
/OPD and I2C Peripherals/OPD_CURRENT: U1.B6 (AIN2); also elsewhere on the board
/OSD3358: SIP A/nRESET: U11.4 (I3); also elsewhere on the board
/OSD3358: SIP B/OSC0_GND: C26.1, C27.1, U1.N15 (OSC0_GND), Y1.2 (G), Y1.4 (G)
/OSD3358: SIP B/OSC0_IN: C26.2, R47.1, U1.P16 (OSC0_IN), Y1.1
/OSD3358: SIP B/OSC0_OUT: C27.2, R47.2, U1.N16 (OSC0_OUT), Y1.3
/OSD3358: SIP B/RADIO_CURRENT: U1.C6 (AIN3); also elsewhere on the board
/OSD3358: SIP B/UHF_FWD_RF_LOG: U1.A8 (AIN0); also elsewhere on the board
/OSD3358: SIP B/UHF_REV_RF_LOG: U1.B8 (AIN1); also elsewhere on the board
/USB_CLI_DM: U1.K16 (USB0_DM), U11.1 (I1); also elsewhere on the board
/USB_CLI_DP: U1.K15 (USB0_DP), U11.3 (I2); also elsewhere on the board
/VIN_USB: C30.2, U1.J16 (USB0_VBUS), U11.5 (VCC); also elsewhere on the board
GND: C30.1, R75.2, U11.2 (GND); also elsewhere on the board
unnamed: C31.2, C32.2, U1.A9 (AGND_ADC), U1.B9 (VREFN)
unnamed: TP41.1 (1_1), U1.C7 (AIN4)
unnamed: TP36.1 (1_1), U1.C8 (AIN5)
unnamed: TP67.1 (1_1), U1.C9 (AIN6)
unnamed: TP69.1 (1_1), U1.D6 (PMIC_MUX_OUT), U1.D7 (AIN7)
unnamed: R77.2, TP95.1 (1_1), U1.E2 (EMU0)
unnamed: R76.2, TP96.1 (1_1), U1.E3 (EMU1)
unnamed: C28.1, C29.1, U1.B5 (OSC1_GND)
unnamed: C28.2, R46.1, U1.A6 (OSC1_IN), Y2.2
unnamed: C29.2, R46.2, U1.A5 (OSC1_OUT), Y2.1
unnamed: TP70.1 (1_1), U1.N13 (PMIC_MUX_IN)
unnamed: C31.1, C32.1, TP59.1 (1_1), U1.A7 (SYS_ADC_1P8V), U1.B7 (VREFP)
unnamed: TP93.1 (1_1), U1.D1 (TCK)
unnamed: TP91.1 (1_1), U1.C1 (TDI)
unnamed: TP92.1 (1_1), U1.C2 (TDO)
unnamed: TP94.1 (1_1), U1.D2 (TMS)
unnamed: R75.1, TP104.1 (1_1), U1.D3 (TRSTN)
unnamed: TP138.1 (1_1), U1.K13 (USB0_CE)
unnamed: TP139.1 (1_1), U1.J15 (USB0_DRVVBUS)
unnamed: TP137.1 (1_1), U1.K14 (USB0_ID)
unnamed: TP71.1 (1_1), U1.L13 (USB1_CE)
unnamed: TP99.1 (1_1), U1.L16 (USB1_DM)
unnamed: TP98.1 (1_1), U1.L15 (USB1_DP)
unnamed: TP72.1 (1_1), U1.M14 (USB1_DRVVBUS)
unnamed: TP97.1 (1_1), U1.L14 (USB1_ID)
unnamed: TP100.1 (1_1), U1.M15 (USB1_VBUS)

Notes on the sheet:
32.768 KHz XO
ALL ADC INPUTS MUST BE <= 1.8V MAXIMUM
To monitor TPS65217 PMIC voltages
SIP pin states ("ZZ", "LL", "ZL", etc) are GPIO states of the pin during and immediately after a reset. See Pg 18-47 in https://www.ti.com/lit/ds/symlink/am3358.pdf
See https://octavosystems.com/faqs/design-oscillator-circuit-osd335x-family-devices/#more-3862 to calculate 24 MHz crystal cap values.
24 MHz XO
32 KHz
Haven't needed JTAG so far
All resistors are 0603 1% AEC-Q200 unless marked. All capacitors are 0603 AEC-Q200 Vw >= 16V X5R or better unless marked.
We've really not used the USB host functionality, so we removed it, especially for the C3. The uSD card can be the main removable storage.
USB Client (goes upstream to PC)
24 MHz
USB ESD protection
SYS_ADC_1P8V and AGND_ADC are connected to SYS_VDD_1P8V and DGND through ferrite beads inside the SiP. Bypass capacitors should be added to reduce noise, if needed.
From Debug Connector (See Connectors Sheet)

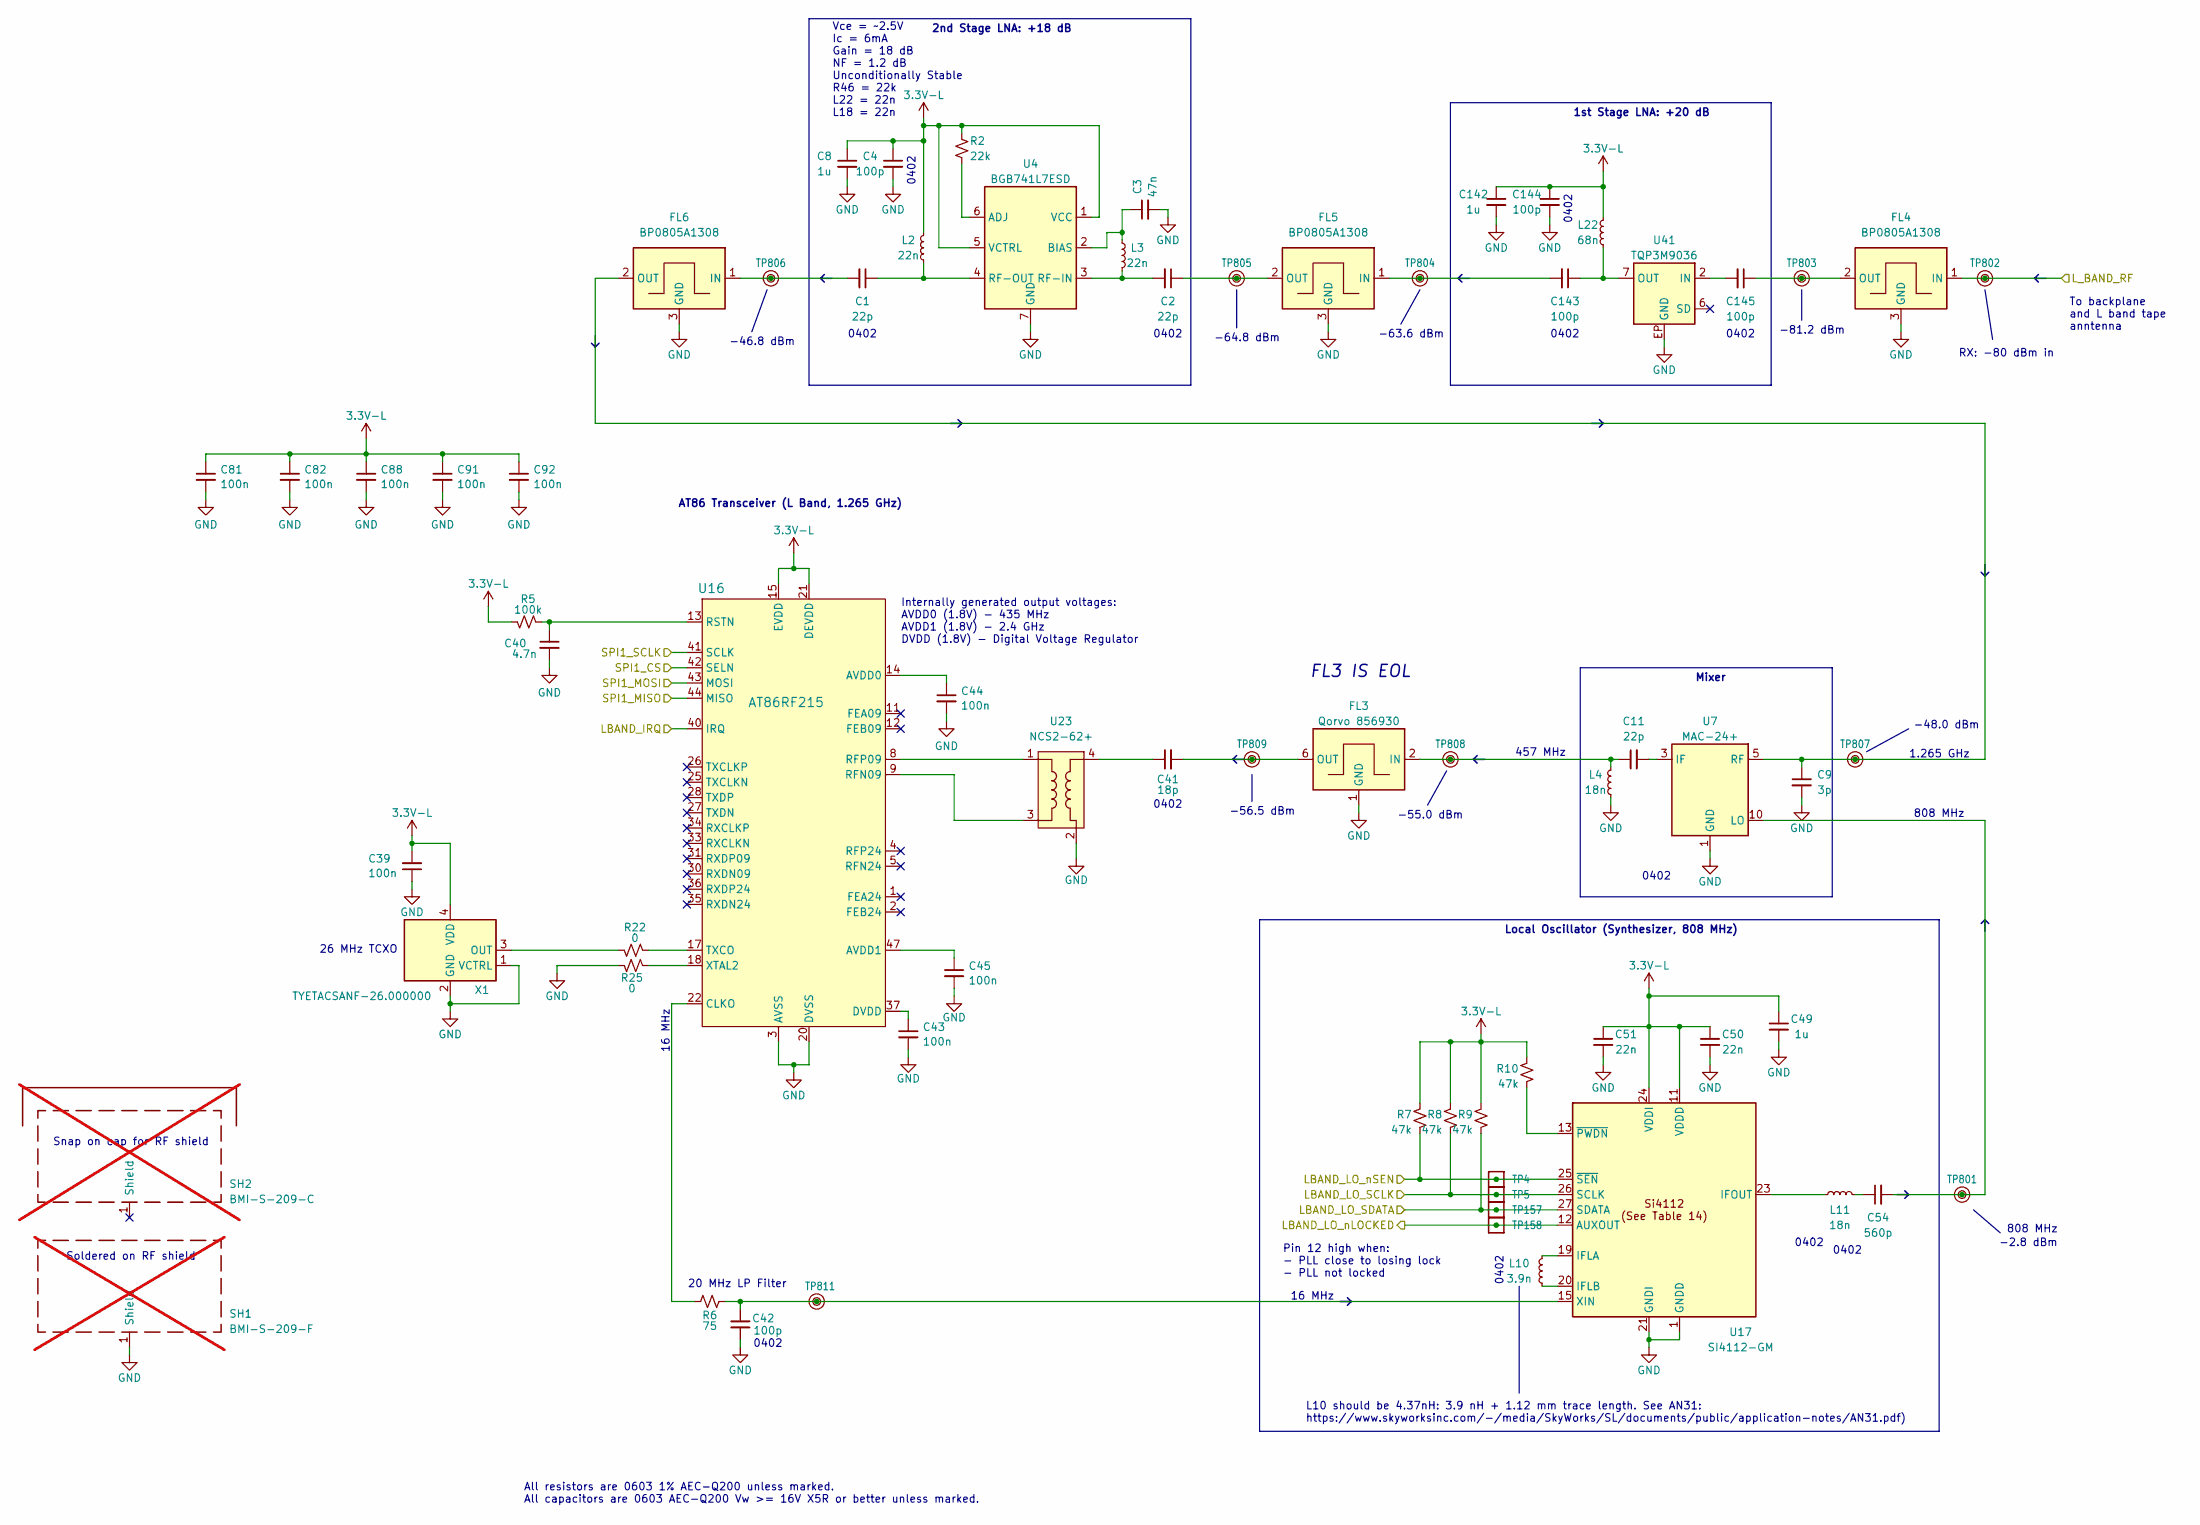
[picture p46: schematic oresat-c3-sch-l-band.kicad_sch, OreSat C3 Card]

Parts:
C1, C2, C11: 22p; 0402-B-NOSILK; MPN CBR04C220J5GACAUTO
C3: 47n; 0603-C-NOSILK; MPN C0603C473K5RACAUTO
C4, C42, C143, C144, C145: 100p; 0402-B-NOSILK; MPN C0402C101J5GACAUTO
C8, C49, C142: 1u; 0603-C-NOSILK; MPN GRT188R71E105KE13D
C9: 3p; 0402-B-NOSILK; MPN GCQ1555C1H3R0CB01D
C39, C43, C44, C45, C81, C82, C88, C91, C92: 100n; 0603-C-NOSILK; MPN C0603C104K5RACAUTO
C40: 4.7n; 0603-C-NOSILK; MPN C0603C472K5RACAUTO
C41: 18p; 0402-B-NOSILK; MPN CBR04C180J5GACAUTO
C50, C51: 22n; 0603-C-NOSILK; MPN C0603C223K1RACAUTO
C54: 560p; 0402-B-NOSILK; MPN C0402C561J5GACAUTO
FL3: Qorvo 856930; 856930-saw-filter; MPN 856930
FL4, FL5, FL6: BP0805A1308; BP0805; MPN BP0805A1308ASTR
L2, L3: 22n; L_0603_1608Metric; MPN LQW18AN22NG0ZD
L4, L11: 18n; L_0402_1005Metric; MPN 0402HP-18NXGL
L10: 3.9n; L_0402_1005Metric; MPN 0402CS-3N9XGL
L22: 68n; L_0603_1608Metric; MPN LQW18AN68NG8ZD
R2: 22k; 0603-C-NOSILK; MPN RMCF0603FT22K0
R5: 100k; 0603-C-NOSILK; MPN RMCF0603FT100K
R6: 75; 0603-C-NOSILK; MPN RMCF0603FT75R0
R7, R8, R9, R10: 47k; 0603-C-NOSILK; MPN RMCF0603FT47K0
R22, R25: 0; 0603-C-NOSILK; MPN RMCF0603ZT0R00
SH1: BMI-S-209-F; Laird_Technologies_BMI-S-209-F_29.36x18.50mm; MPN BMI-S-209-F; not fitted
SH2: BMI-S-209-C; MPN BMI-S-209-C; not fitted
TP4, TP5, TP157, TP158: Test-Point; TestPoint_Pad_D1.0mm
TP801, TP802, TP803, TP804, TP805, TP806, TP807, TP808, TP809, TP811: TestPoint_RF_Probe
U4: BGB741L7ESD; Infineon-PG-TSLP-7-LNA; MPN BGB741L7ESDE6327XTSA1‎
U7: MAC-24+; MPN MAC-24+
U16: AT86RF215; QFN-48-1EP_7x7mm_P0.5mm_EP5.6x5.6mm; MPN AT86RF215-ZUR
U17: SI4112-GM; QFN-28-1EP_5x5mm_P0.5mm_EP3.35x3.35mm_ThermalVias; MPN SI4112-D-GM
U23: NCS2-62+; 2450FB15A050E_JOT; MPN NCS2-62+
U41: TQP3M9036; U-Qorvo-TQP3M9036-QFN-8-MO-220E; MPN TQP3M9036
X1: TYETACSANF-26.000000; X_TCXO_SMD_Taitien_2.5x2.0mm; MPN TYETACSANF-26.000000

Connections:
3.3V-L: C4.1, C8.1, C39.2, C49.1, C50.1, C51.1, C81.1, C82.1, C88.1, C91.1, C92.1, C142.1, C144.1, L2.1, L22.1, R2.1, R5.2, R7.1, R8.1, R9.1, R10.1, U4.1 (VCC), U4.5 (VCTRL), U16.15 (EVDD), U16.21 (DEVDD), U16.29 (DEVDD), U16.39 (DEVDD), U16.46 (EVDD), U17.11 (VDDD), U17.17 (VDDD), U17.24 (VDDI), X1.4 (VDD); also elsewhere on the board
/L Band/LBAND_IRQ: U16.40 (IRQ); also elsewhere on the board
/L Band/LBAND_LO_SCLK: R8.2, TP5.1 (1_1), U17.26 (SCLK); also elsewhere on the board
/L Band/LBAND_LO_SDATA: R9.2, TP157.1 (1_1), U17.27 (SDATA); also elsewhere on the board
/L Band/LBAND_LO_nLOCKED: TP158.1 (1_1), U17.12 (AUXOUT); also elsewhere on the board
/L Band/LBAND_LO_nSEN: R7.2, TP4.1 (1_1), U17.25 (~SEN); also elsewhere on the board
/L Band/SPI1_CS: U16.42 (SELN); also elsewhere on the board
/L Band/SPI1_MISO: U16.44 (MISO); also elsewhere on the board
/L Band/SPI1_MOSI: U16.43 (MOSI); also elsewhere on the board
/L Band/SPI1_SCLK: U16.41 (SCLK); also elsewhere on the board
/L_BAND_RF: FL4.1 (IN), TP802.1 (1_1); also elsewhere on the board
GND: C3.2, C4.2, C8.2, C9.2, C39.1, C40.2, C42.2, C43.2, C44.2, C45.2, C49.2, C50.2, C51.2, C81.2, C82.2, C88.2, C91.2, C92.2, C142.2, C144.2, FL3.1 (GND), FL3.3 (GND), FL3.4 (GND), FL3.5 (GND), FL3.7 (GND), FL3.8 (GND), FL4.3 (GND), FL4.4 (GND), FL5.3 (GND), FL5.4 (GND), FL6.3 (GND), FL6.4 (GND), L4.2, R25.2, SH1.1 (Shield_1), U4.7 (GND), U7.1 (GND), U7.2 (GND), U7.4 (GND), U7.6 (GND), U7.7 (GND), U7.8 (GND), U7.9 (GND), U16.3 (AVSS), U16.6 (AVSS), U16.7 (AVSS), U16.10 (AVSS), U16.16 (AVSS), U16.19 (AVSS), U16.20 (DVSS), U16.23 (DVSS), U16.24 (DVSS), U16.32 (DVSS), U16.38 (DVSS), U16.45 (AVSS), U16.48 (AVSS), U16.49 (AVSS), U17.1 (GNDD), U17.2 (GNDD), U17.3 (GNDD), U17.4 (GNDD), U17.5 (GNDD), U17.6 (GNDD), U17.7 (GNDD), U17.8 (GNDD), U17.9 (GNDD), U17.10 (GNDD), U17.14 (GNDD), U17.16 (GNDD), U17.18 (GNDD), U17.21 (GNDI), U17.22 (GNDI), U17.28 (GNDD), U17.29 (GNDD), U23.2 (GND), U23.6 (GND), U41.EP (GND), X1.1 (VCTRL), X1.2 (GND); also elsewhere on the board
unnamed: C41.1, U23.4
unnamed: C54.1, L11.2
unnamed: C11.1, FL3.2 (IN), L4.1, TP808.1 (1_1)
unnamed: C41.2, FL3.6 (OUT), TP809.1 (1_1)
unnamed: C145.1, FL4.2 (OUT), TP803.1 (1_1)
unnamed: C143.2, FL5.1 (IN), TP804.1 (1_1)
unnamed: C2.1, FL5.2 (OUT), TP805.1 (1_1)
unnamed: C1.2, FL6.1 (IN), TP806.1 (1_1)
unnamed: C9.1, FL6.2 (OUT), TP807.1 (1_1), U7.5 (RF)
unnamed: R2.2, U4.6 (ADJ)
unnamed: C3.1, L3.1, U4.2 (BIAS)
unnamed: C2.2, L3.2, U4.3 (RF-IN)
unnamed: C1.1, L2.2, U4.4 (RF-OUT)
unnamed: C11.2, U7.3 (IF)
unnamed: C54.2, TP801.1 (1_1), U7.10 (LO)
unnamed: C44.1, U16.14 (AVDD0)
unnamed: C45.1, U16.47 (AVDD1)
unnamed: R6.1, U16.22 (CLKO)
unnamed: C43.1, U16.37 (DVDD)
unnamed: U16.9 (RFN09), U23.3
unnamed: U16.8 (RFP09), U23.1
unnamed: C40.1, R5.1, U16.13 (RSTN)
unnamed: R22.1, U16.17 (TXCO)
unnamed: R25.1, U16.18 (XTAL2)
unnamed: L10.1, U17.19 (IFLA)
unnamed: L10.2, U17.20 (IFLB)
unnamed: L11.1, U17.23 (IFOUT)
unnamed: C42.1, R6.2, TP811.1 (1_1), U17.15 (XIN)
unnamed: R10.2, U17.13 (~PWDN)
unnamed: C145.2, U41.2 (IN)
unnamed: C143.1, L22.2, U41.7 (OUT)
unnamed: R22.2, X1.3 (OUT)

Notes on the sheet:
0402
-56.5 dBm
-46.8 dBm
Pin 12 high when: - PLL close to losing lock - PLL not locked
RX: -80 dBm in
FL3 IS EOL
AT86 Transceiver (L Band, 1.265 GHz)
Internally generated output voltages: AVDD0 (1.8V) - 435 MHz AVDD1 (1.8V) - 2.4 GHz DVDD (1.8V) - Digital Voltage Regulator
Vce = ~2.5V Ic = 6mA Gain = 18 dB NF = 1.2 dB Unconditionally Stable R46 = 22k L22 = 22n L18 = 22n
L10 should be 4.37nH: 3.9 nH + 1.12 mm trace length. See AN31: https://www.skyworksinc.com/-/media/SkyWorks/SL/documents/public/application-notes/AN31.pdf)
2nd Stage LNA: +18 dB
1.265 GHz
-2.8 dBm
808 MHz
1st Stage LNA: +20 dB
26 MHz TCXO
-81.2 dBm
To backplane and L band tape anntenna
All resistors are 0603 1% AEC-Q200 unless marked. All capacitors are 0603 AEC-Q200 Vw >= 16V X5R or better unless marked.
457 MHz
-55.0 dBm
-64.8 dBm
20 MHz LP Filter
-63.6 dBm
16 MHz
Snap on cap for RF shield
Mixer
Local Oscillator (Synthesizer, 808 MHz)
Soldered on RF shield
-48.0 dBm

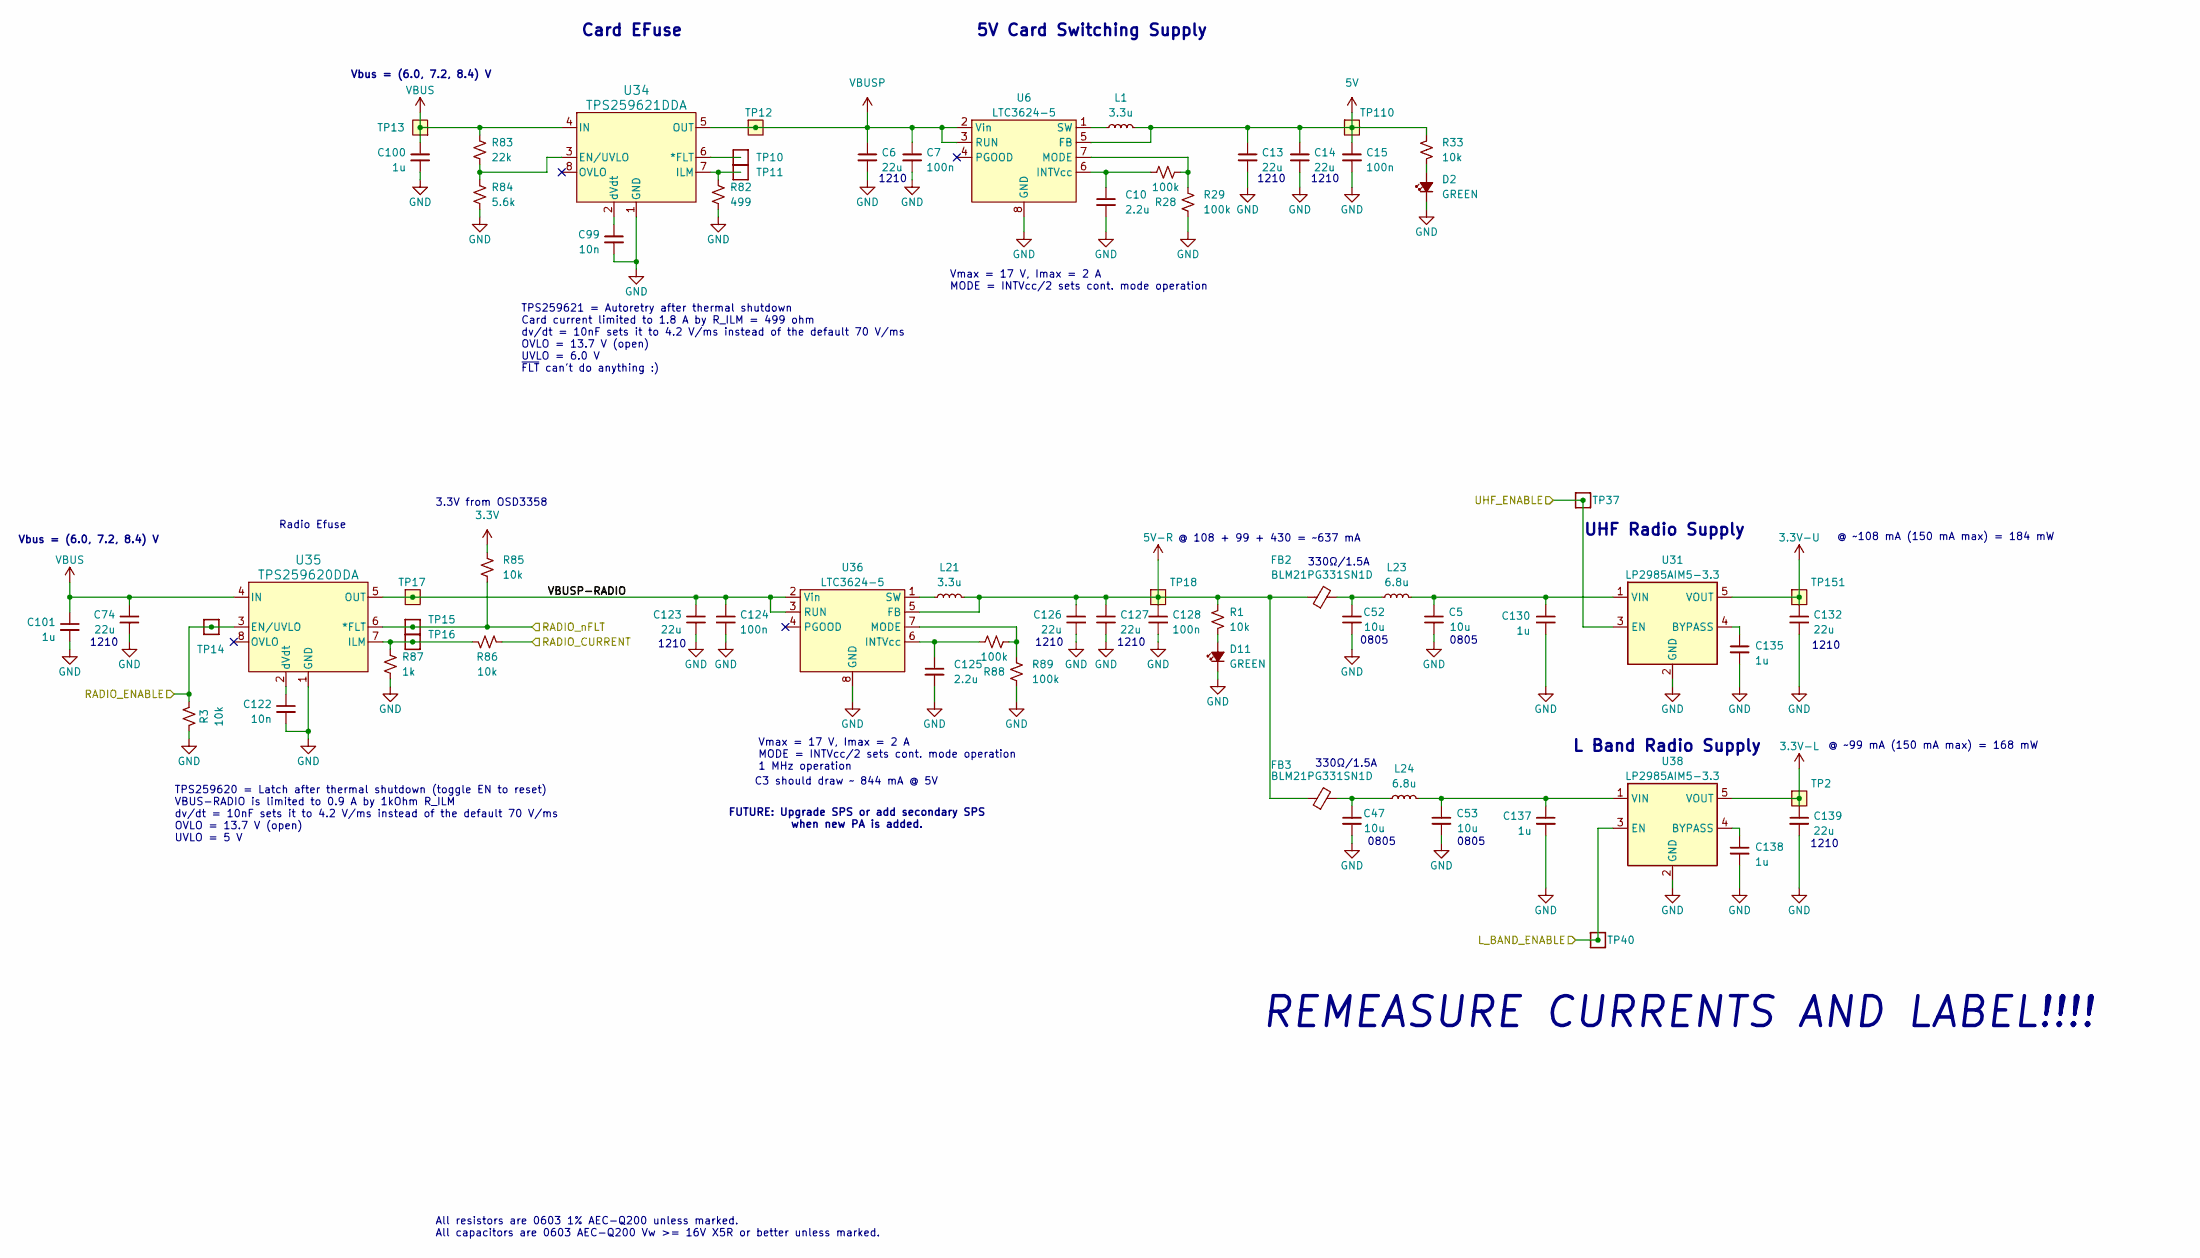
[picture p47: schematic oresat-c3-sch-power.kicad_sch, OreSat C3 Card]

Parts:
C5, C47, C52, C53: 10u; 0805-C-NOSILK; MPN GRT21BC71E106KE13K
C6, C13, C14, C74, C123, C126, C127, C132, C139: 22u; C_1210_3225Metric; MPN TMK325B7226KMHP
C7, C15, C124, C128: 100n; 0603-C-NOSILK; MPN C0603C104K5RACAUTO
C10, C125: 2.2u; 0603-C-NOSILK; MPN GRT188C71E225KE13D
C99, C122: 10n; 0603-C-NOSILK; MPN C0603C103J5RACAUTO
C100, C101, C130, C135, C137, C138: 1u; 0603-C-NOSILK; MPN GRT188R71E105KE13D
D2, D11: GREEN; LED_0603_1608Metric; MPN 150060GS75000
FB2, FB3: BLM21PG331SN1D; R_0805_2012Metric; MPN BLM21PG331SN1D
L1, L21: 3.3u; L_ECS-MPI4040; MPN ECS-MPI4040R3-3R3-R
L23, L24: 6.8u; L_ECS-MPI4040; MPN ECS-MPI4040R4-6R8-R
R1, R3, R33, R85, R86: 10k; 0603-C-NOSILK; MPN RMCF0603FT10K0
R28, R29, R88, R89: 100k; 0603-C-NOSILK; MPN RMCF0603FT100K
R82: 499; 0603-C-NOSILK; MPN RMCF0603FT499R
R83: 22k; 0603-C-NOSILK; MPN RMCF0603FT22K0
R84: 5.6k; 0603-C-NOSILK; MPN RMCF0603FT5K60
R87: 1k; 0603-C-NOSILK; MPN RMCF0603FT1K00
TP2, TP12, TP13, TP17, TP18, TP110, TP151: Test-Point; TestPoint-0.75mm-th
TP10, TP11, TP14, TP15, TP16, TP37, TP40: Test-Point; TestPoint_Pad_D1.0mm
U6, U36: LTC3624-5; DFN-8-1EP_3x3mm_P0.5mm_EP1.65x2.38mm_ThermalVias0.3mm; MPN LTC3624IDD-5#PBF
U31, U38: LP2985AIM5-3.3; SOT-23-5; MPN LP2985AIM5-3.3/NOPB
U34: TPS259621DDA; Texas_R-PDSO-G8_EP2.95x4.9mm_Mask2.4x3.1mm_ThermalVias; MPN TPS259621DDAT
U35: TPS259620DDA; Texas_R-PDSO-G8_EP2.95x4.9mm_Mask2.4x3.1mm_ThermalVias; MPN TPS259620DDAT

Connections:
3.3V: R85.1; also elsewhere on the board
3.3V-L: C139.1, TP2.1 (1_1), U38.5 (VOUT); also elsewhere on the board
3.3V-U: C132.1, TP151.1 (1_1), U31.5 (VOUT); also elsewhere on the board
5V: C13.1, C14.1, C15.1, L1.2, R33.2, TP110.1 (1_1), U6.5 (FB); also elsewhere on the board
5V-R: C126.1, C127.1, C128.1, FB2.1, FB3.1, L21.2, R1.2, TP18.1 (1_1), U36.5 (FB); also elsewhere on the board
/OSD3358: SIP B/RADIO_CURRENT: R86.1; also elsewhere on the board
/OSD3358: SIP C/L_BAND_ENABLE: TP40.1 (1_1), U38.3 (EN); also elsewhere on the board
/OSD3358: SIP C/RADIO_nFLT: R85.2, TP15.1 (1_1), U35.6 (*FLT); also elsewhere on the board
/OSD3358: SIP C/UHF_ENABLE: TP37.1 (1_1), U31.3 (EN); also elsewhere on the board
/OSD3358: SIP D/RADIO_ENABLE: R3.1, TP14.1 (1_1), U35.3 (EN/UVLO); also elsewhere on the board
/Power/VBUSP-RADIO: C123.1, C124.1, TP17.1 (1_1), U35.5 (OUT), U36.2 (Vin), U36.3 (RUN)
GND: C5.2, C6.2, C7.2, C10.2, C13.2, C14.2, C15.2, C47.2, C52.2, C53.2, C74.2, C99.2, C100.2, C101.2, C122.2, C123.2, C124.2, C125.2, C126.2, C127.2, C128.2, C130.2, C132.2, C135.2, C137.2, C138.2, C139.2, D2.1 (K), D11.1 (K), R3.2, R29.2, R82.2, R84.2, R87.2, R89.2, U6.8 (GND), U6.9 (GND), U31.2 (GND), U34.1 (GND), U34.9 (GND), U35.1 (GND), U35.9 (GND), U36.8 (GND), U36.9 (GND), U38.2 (GND); also elsewhere on the board
unnamed: C47.1, FB3.2, L24.1
unnamed: C52.1, FB2.2, L23.1
unnamed: D2.2 (A), R33.1
unnamed: D11.2 (A), R1.1
unnamed: C10.1, R28.1, U6.6 (INTVcc)
unnamed: R28.2, R29.1, U6.7 (MODE)
unnamed: L1.1, U6.1 (SW)
unnamed: C135.1, U31.4 (BYPASS)
unnamed: C5.1, C130.1, L23.2, U31.1 (VIN)
unnamed: TP10.1 (1_1), U34.6 (*FLT)
unnamed: R83.2, R84.1, U34.3 (EN/UVLO)
unnamed: R82.1, TP11.1 (1_1), U34.7 (ILM)
unnamed: C99.1, U34.2 (dVdt)
unnamed: R86.2, R87.1, TP16.1 (1_1), U35.7 (ILM)
unnamed: C122.1, U35.2 (dVdt)
unnamed: C125.1, R88.1, U36.6 (INTVcc)
unnamed: R88.2, R89.1, U36.7 (MODE)
unnamed: L21.1, U36.1 (SW)
unnamed: C138.1, U38.4 (BYPASS)
unnamed: C53.1, C137.1, L24.2, U38.1 (VIN)
VBUS: C74.1, C100.1, C101.1, R83.1, TP13.1 (1_1), U34.4 (IN), U35.4 (IN); also elsewhere on the board
VBUSP: C6.1, C7.1, TP12.1 (1_1), U6.2 (Vin), U6.3 (RUN), U34.5 (OUT)

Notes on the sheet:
REMEASURE CURRENTS AND LABEL!!!!
330Ω/1.5A
1210
Vbus = (6.0, 7.2, 8.4) V
Radio Efuse
5V Card Switching Supply
Vmax = 17 V, Imax = 2 A MODE = INTVcc/2 sets cont. mode operation 1 MHz operation
0805
FUTURE: Upgrade SPS or add secondary SPS when new PA is added.
C3 should draw ~ 844 mA @ 5V
3.3V from OSD3358
All resistors are 0603 1% AEC-Q200 unless marked. All capacitors are 0603 AEC-Q200 Vw >= 16V X5R or better unless marked.
UHF Radio Supply
@ ~99 mA (150 mA max) = 168 mW
@ 108 + 99 + 430 = ~637 mA
Vmax = 17 V, Imax = 2 A MODE = INTVcc/2 sets cont. mode operation
TPS259621 = Autoretry after thermal shutdown Card current limited to 1.8 A by R_ILM = 499 ohm dv/dt = 10nF sets it to 4.2 V/ms instead of the default 70 V/ms OVLO = 13.7 V (open) UVLO = 6.0 V ~{FLT} can't do anything :)
Card EFuse
@ ~108 mA (150 mA max) = 184 mW
TPS259620 = Latch after thermal shutdown (toggle EN to reset) VBUS-RADIO is limited to 0.9 A by 1kOhm R_ILM dv/dt = 10nF sets it to 4.2 V/ms instead of the default 70 V/ms OVLO = 13.7 V (open) UVLO = 5 V
L Band Radio Supply

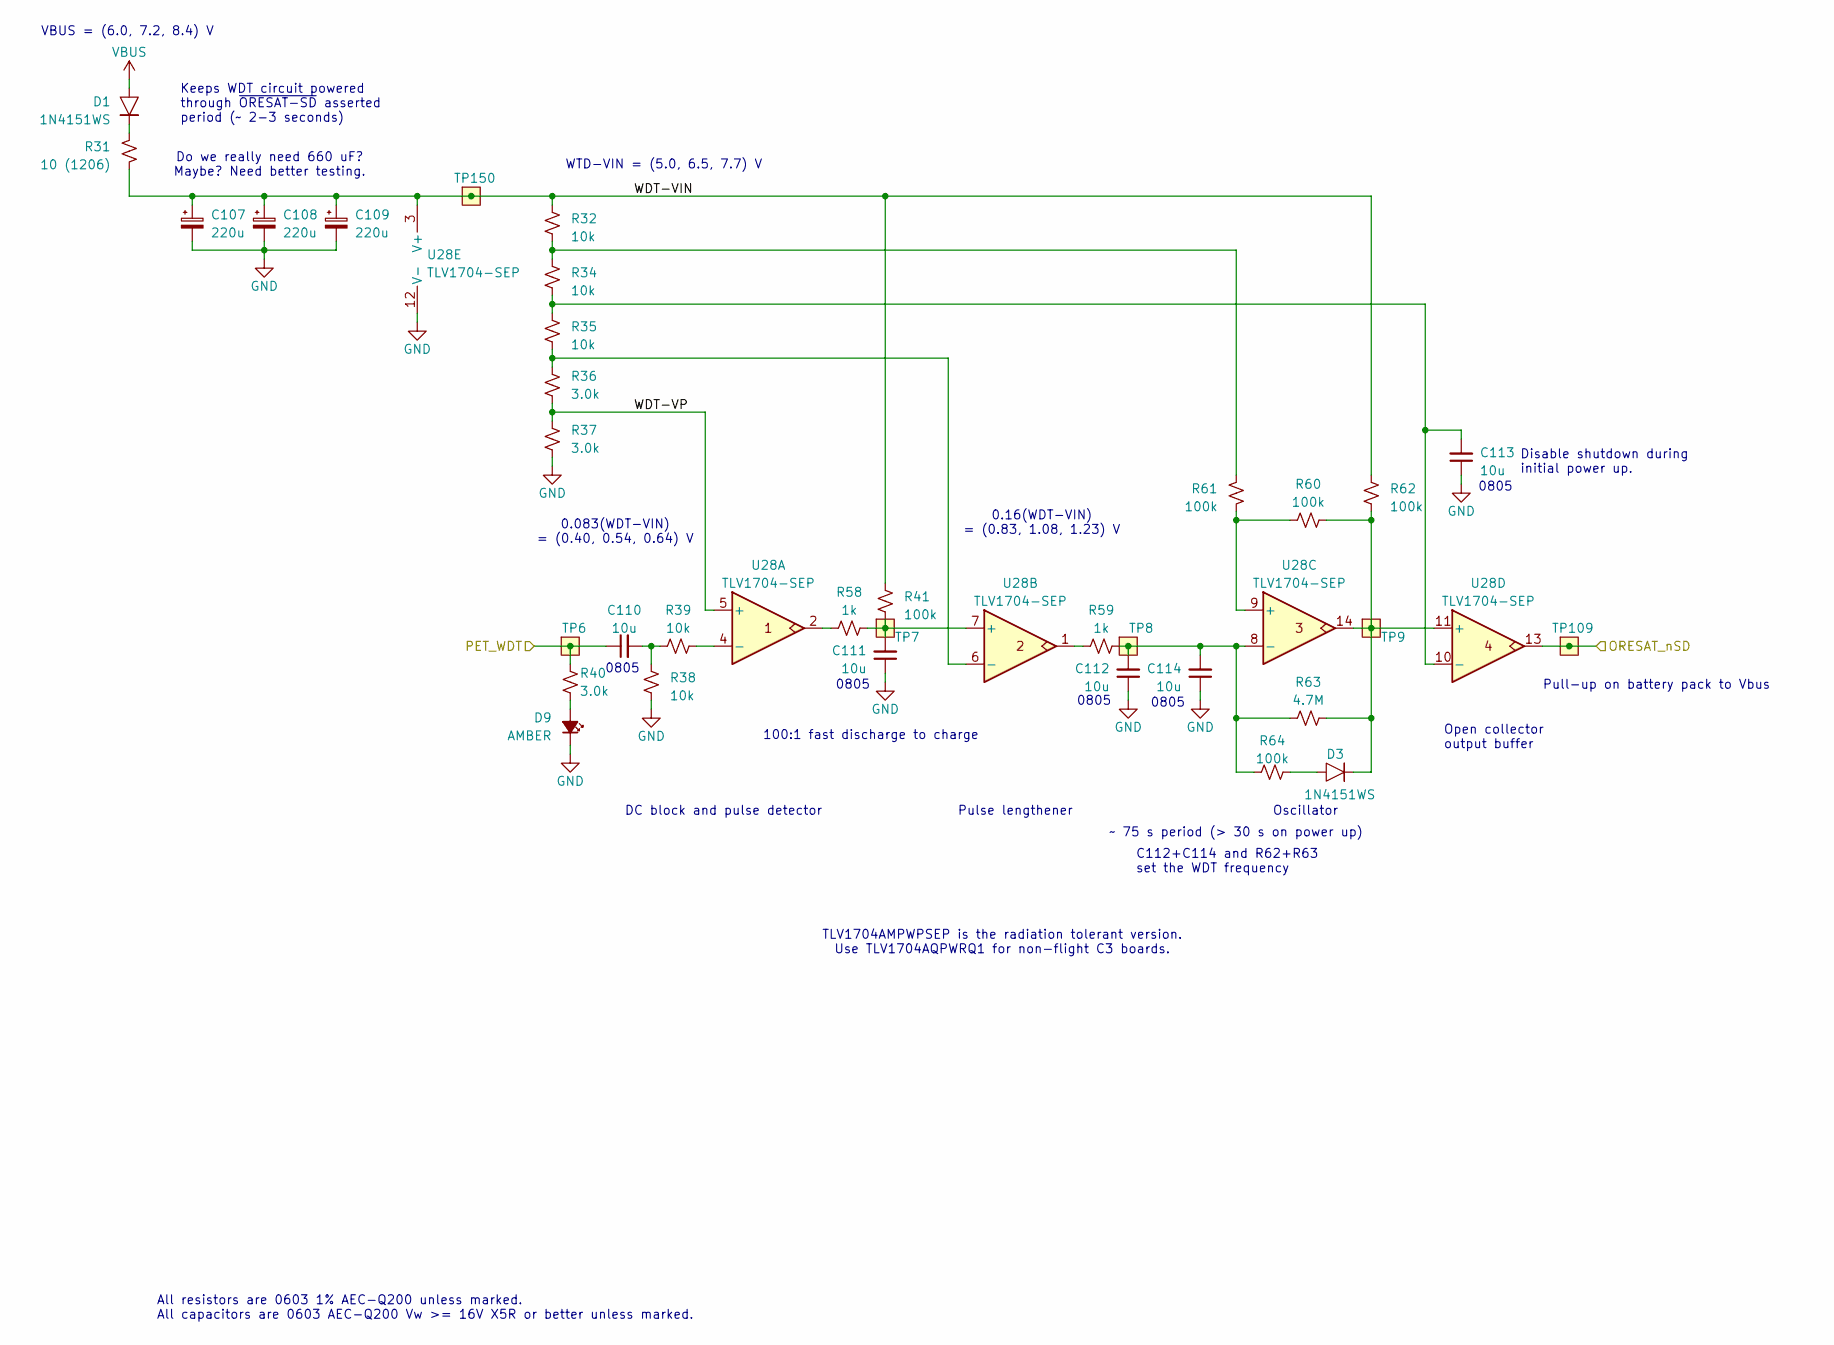
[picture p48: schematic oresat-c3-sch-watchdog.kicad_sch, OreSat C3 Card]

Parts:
C107, C108, C109: 220u; CP_EIA-7343-31_Kemet-D; MPN TBJE227K016LBSZ0000
C110, C111, C112, C113, C114: 10u; 0805-C-NOSILK; MPN GRT21BC71E106KE13K
D1, D3: 1N4151WS; D_SOD-323; MPN 1N4151WS-E3-08
D9: AMBER; LED_0603_1608Metric; MPN 150060AS75000
R31: 10 (1206); 1206-C; MPN RMCF1206FT10R0
R32, R34, R35, R38, R39: 10k; 0603-C-NOSILK; MPN RMCF0603FT10K0
R36, R37, R40: 3.0k; 0603-C-NOSILK; MPN RMCF0603FT3K00
R41, R60, R61, R62, R64: 100k; 0603-C-NOSILK; MPN RMCF0603FT100K
R58, R59: 1k; 0603-C-NOSILK; MPN RMCF0603FT1K00
R63: 4.7M; 0603-C-NOSILK; MPN RMCF0603FT4M70
TP6, TP7, TP8, TP9, TP109, TP150: TestPoint-MinTH; TestPoint-0.75mm-th
U28: TLV1704-SEP; TSSOP-14_4.4x5mm_P0.65mm; MPN TLV1704AMPWPSEP

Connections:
/ORESAT_nSD: TP109.1 (1_1), U28.13; also elsewhere on the board
/OSD3358: SIP D/PET_WDT: C110.1, R40.1, TP6.1 (1_1); also elsewhere on the board
/Watchdog/WDT-VIN: C107.1, C108.1, C109.1, R31.2, R32.1, R41.1, R62.2, TP150.1 (1_1), U28.3 (V+)
/Watchdog/WDT-VP: R36.2, R37.1, U28.5 (+)
GND: C107.2, C108.2, C109.2, C111.1, C112.1, C113.1, C114.1, D9.1 (K), R37.2, R38.2, U28.12 (V-); also elsewhere on the board
unnamed: C110.2, R38.1, R39.1
unnamed: D1.1, R31.1
unnamed: D3.2, R64.1
unnamed: D9.2 (A), R40.2
unnamed: R32.2, R34.1, R61.2
unnamed: R58.1, U28.2
unnamed: R59.1, U28.1
unnamed: R39.2, U28.4 (-)
unnamed: C111.2, R41.2, R58.2, TP7.1 (1_1), U28.7 (+)
unnamed: R35.2, R36.1, U28.6 (-)
unnamed: R60.1, R61.1, U28.9 (+)
unnamed: C112.2, C114.2, R59.2, R63.2, R64.2, TP8.1 (1_1), U28.8 (-)
unnamed: D3.1, R60.2, R62.1, R63.1, TP9.1 (1_1), U28.11 (+), U28.14
unnamed: C113.2, R34.2, R35.1, U28.10 (-)
VBUS: D1.2; also elsewhere on the board

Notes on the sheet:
100:1 fast discharge to charge
0805
VBUS = (6.0, 7.2, 8.4) V
Pulse lengthener
Oscillator
C112+C114 and R62+R63 set the WDT frequency
Do we really need 660 uF? Maybe? Need better testing.
WTD-VIN = (5.0, 6.5, 7.7) V
DC block and pulse detector
Open collector output buffer
Pull-up on battery pack to Vbus
0.16(WDT-VIN) = (0.83, 1.08, 1.23) V
All resistors are 0603 1% AEC-Q200 unless marked. All capacitors are 0603 AEC-Q200 Vw >= 16V X5R or better unless marked.
Disable shutdown during initial power up.
Keeps WDT circuit powered through ~{ORESAT-SD} asserted period (~ 2-3 seconds)
TLV1704AMPWPSEP is the radiation tolerant version. Use TLV1704AQPWRQ1 for non-flight C3 boards.
~ 75 s period (> 30 s on power up)
0.083(WDT-VIN) = (0.40, 0.54, 0.64) V

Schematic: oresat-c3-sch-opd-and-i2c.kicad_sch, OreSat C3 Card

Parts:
C79, C129: 1u; 0603-C-NOSILK; MPN GRT188R71E105KE13D
C115: 100u; C_1210_3225Metric; MPN GRT32ER60J107ME13L
C116, C117, C131: 100n; 0603-C-NOSILK; MPN C0603C104K5RACAUTO
D10: 1N4151WS; D_SOD-323; MPN 1N4151WS-E3-08
D12: GREEN; LED_0603_1608Metric; MPN 150060GS75000
Q1: DMP2035UQ-7; SOT-23; MPN DMP2035UQ-7
R49, R51, R66, R78, R79: 10k; 0603-C-NOSILK; MPN RMCF0603FT10K0
R52: 22k; 0603-C-NOSILK; MPN RMCF0603FT22K0
R67: 150; 0603-C-NOSILK; MPN RMCF0603FT150R
R68, R80, R92, R93: 4.7k; 0603-C-NOSILK; MPN RMCF0603FT4K70
TP61, TP141, TP148, TP149, TP160, TP164, TP165, TP166, TP167, TP168, TP169: Test-Point; TestPoint_Pad_D1.0mm
TP163: TestPoint-MinTH; TestPoint-0.75mm-th
U12: RCLAMP0504FB; SOT-363_SC-70-6; MPN RCLAMP0504FBTCT
U13: MAX892LEUA+T; LINEAR-MSOP-8-AND-MAXIM-UMAX-8-21-0036; MPN MAX892LEUA+T
U24: RV-3028-C7; MicroCrystal_C7_SON-8_1.5x3.2mm_P0.9mm; MPN RV-3028-C7 32.768KHZ 1PPM-TA-QA
U30: FM24CL64B-GTR; SOIC-8_3.9x4.9mm_P1.27mm; MPN FM24CL64B-G
U37: LTC4300A-1; LINEAR-MSOP-8-AND-MAXIM-UMAX-8-21-0036; MPN LTC4300A-1IMS8#TRPBF

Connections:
3.3V: C79.1, Q1.2 (S), R49.1, R51.1, U13.1 (IN), U13.2 (IN_2); also elsewhere on the board
/OPD and I2C Peripherals/I2C2_SYS_DISABLE: Q1.1 (G), R66.1; also elsewhere on the board
/OPD and I2C Peripherals/I2C2_SYS_SCL: R80.2, TP168.1 (1_1), U24.3 (SCL), U30.6 (SCL), U37.2 (SCLOUT); also elsewhere on the board
/OPD and I2C Peripherals/I2C2_SYS_SDA: R68.2, TP169.1 (1_1), U24.4 (SDA), U30.5 (SDA), U37.7 (SDAOUT); also elsewhere on the board
/OPD and I2C Peripherals/OPD_CURRENT: R52.1, TP61.1 (1_1), U13.5 (SET); also elsewhere on the board
/OPD and I2C Peripherals/OPD_nENABLE: R49.2, TP167.1 (1_1), U13.3 (~ON); also elsewhere on the board
/OPD and I2C Peripherals/OPD_nFAULT: R51.2, TP166.1 (1_1), U13.6 (~FAULT); also elsewhere on the board
/OPD_PWR: C129.1, C131.1, R78.2, R92.1, R93.1, TP163.1 (1_1), U12.5 (VCC), U13.7 (OUT_2), U13.8 (OUT), U37.1 (ENABLE), U37.8 (VCC); also elsewhere on the board
/OPD_SCL: R92.2, TP164.1 (1_1), U12.1 (I1), U37.3 (SCLIN); also elsewhere on the board
/OPD_SDA: R93.2, TP165.1 (1_1), U12.3 (I2), U37.6 (SDAIN); also elsewhere on the board
GND: C79.2, C115.2, C116.2, C117.2, C129.2, C131.2, D12.1 (K), R52.2, R66.2, R79.2, U12.2 (GND), U13.4 (GND), U24.5 (VSS), U30.1 (A0), U30.2 (A1), U30.3 (A2), U30.4 (VSS), U37.4 (GND); also elsewhere on the board
unnamed: D10.2, R67.2
unnamed: D12.2 (A), R78.1
unnamed: C116.1, C117.1, Q1.3 (D), R67.1, R68.1, R80.1, U24.7 (VDD), U30.8 (VDD)
unnamed: TP141.1 (1_1), U24.1 (CLKO)
unnamed: R79.1, TP149.1 (1_1), U24.8 (EVI)
unnamed: C115.1, D10.1, U24.6 (VBKP)
unnamed: TP148.1 (1_1), U24.2 (~INT)
unnamed: TP160.1 (1_1), U30.7 (WP)

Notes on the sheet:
To OPD. See Connectors sheet.
Should not go above 1.4V
8k x 8 (64kb) I2C FRAM
FRAM
All resistors are 0603 1% AEC-Q200 unless marked. All capacitors are 0603 AEC-Q200 Vw >= 16V X5R or better unless marked.
Normally on; asserting I2C_SYS_DISABLE will turn off this subsystem.
IMPORTANT: To power down RTC/FRAM, OPD_PWR must be turned off as well to prevent pullup voltage bleeding through the LTC4300A-1.
Limits OPD_PWR to 54 mA
I2C pullups provided by RTC/FRAM power PFET above.
Murata GRT32ER60J107ME13L 100uF 20% 6.3V X5R 1210 Capacitor
1210
HOW LONG WILL IT KEEP?
RTC
OreSat Power Domain (OPD) Control

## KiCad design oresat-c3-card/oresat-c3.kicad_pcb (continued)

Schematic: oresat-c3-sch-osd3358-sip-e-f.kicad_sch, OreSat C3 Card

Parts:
TP19, TP20, TP21, TP22: Test-Point; TestPoint_Pad_D1.0mm
U1: OSD3358-1G-ISM; U-Octavo-OSD335X-BGA-256; MPN OSD3358-512M-BSM

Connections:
GND: U1.D8 (DGND@1), U1.D9 (DGND@2), U1.E5 (DGND@3), U1.E6 (DGND@4), U1.E7 (DGND@5), U1.E8 (DGND@6), U1.E9 (DGND@7), U1.E10 (DGND@8), U1.E11 (DGND@9), U1.E12 (DGND@10), U1.F5 (DGND@11), U1.F12 (DGND@12), U1.G5 (DGND@13), U1.G12 (DGND@14), U1.H4 (DGND@15), U1.H5 (DGND@16), U1.H12 (DGND@17), U1.H13 (DGND@18), U1.J4 (DGND@19), U1.J5 (DGND@20), U1.J12 (DGND@21), U1.J13 (DGND@22), U1.K5 (DGND@23), U1.K12 (DGND@24), U1.L5 (DGND@25), U1.L12 (DGND@26), U1.M5 (DGND@27), U1.M6 (DGND@28), U1.M7 (DGND@29), U1.M8 (DGND@30), U1.M9 (DGND@31), U1.M10 (DGND@32), U1.M11 (DGND@33), U1.M12 (DGND@34), U1.N8 (DGND@35), U1.N9 (DGND@36); also elsewhere on the board
unnamed: TP19.1 (1_1), U1.F4 (VDDS_DDR)
unnamed: TP22.1 (1_1), U1.G13 (VDDS_PLL)
unnamed: TP20.1 (1_1), U1.G4 (VDD_CORE)
unnamed: TP21.1 (1_1), U1.F13 (VDD_MPU)

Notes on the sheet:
All resistors are 0603 1% AEC-Q200 unless marked. All capacitors are 0603 AEC-Q200 Vw >= 16V X5R or better unless marked.

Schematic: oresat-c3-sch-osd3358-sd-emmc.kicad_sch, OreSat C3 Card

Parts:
C16, C25: 10u; 0805-C-NOSILK; MPN GRT21BC71E106KE13K
C17, C18, C48: 100n; 0603-C-NOSILK; MPN C0603C104K5RACAUTO
C19, C20, C21, C22, C23, C24: 1u; 0603-C-NOSILK; MPN GRT188R71E105KE13D
D4, D5, D6, D7: BLUE; LED_0603_1608Metric; MPN 150060BS75000
J5: DM3BT-DSF-PEJS; J-Hirose-DM3BT-DSF-PEJS; MPN DM3BT-DSF-PEJS
R30, R42, R43, R44, R45, R90: 10k; 0603-C-NOSILK; MPN RMCF0603FT10K0
R69, R70, R71: 10k; Panasonic_Resistor_Array_EXBA10; MPN EXB-A10P103J
R91, R94: 150; 0603-C-NOSILK; MPN RMCF0603FT150R
TP27, TP33, TP34, TP35, TP38, TP39, TP42, TP46, TP47, TP48, TP64, TP65, TP66, TP68, TP89, TP124, TP126, TP162, TP170: Test-Point; TestPoint_Pad_D1.0mm
U1: OSD3358-1G-ISM; U-Octavo-OSD335X-BGA-256; MPN OSD3358-512M-BSM
U8: TCAN330; SOT-23-8; MPN TCAN330GDCNT
U9: SFEM016GB1EA1TO-I-GE-121-STD; BGA-153(11.5X13)(EMMC-BA); MPN SFEM064GB2ED1TO-A-6F-111-STD
U42: 74LVC2G34; SOT-363_SC-70-6; MPN 74LVC2G34GW-Q100,1

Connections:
3.3V: C16.1, C17.1, C18.1, C21.1, C22.1, C23.1, C24.1, C25.1, C48.2, J5.4 (VDD), R69.5 (55), R69.10 (55), R70.5 (55), R70.10 (55), R71.5 (55), R71.10 (55), U8.3 (VCC), U9.C6 (VDDQ), U9.E6 (VDDIO), U9.F5 (VDDIO), U9.J10 (VDDIO), U9.K9 (VDDIO), U9.M4 (VDDQ), U9.N4 (VDDQ), U9.P3 (VDDQ), U9.P5 (VDDQ), U42.5 (VCC); also elsewhere on the board
/C3-UART-RX: U1.A12 (UART0_RXD); also elsewhere on the board
/C3-UART-TX: U1.B12 (UART0_TXD); also elsewhere on the board
/CAN1_H: U8.7 (CANH); also elsewhere on the board
/CAN1_L: U8.6 (CANL); also elsewhere on the board
/L Band/LBAND_IRQ: U1.R16 (GPMC_WPN); also elsewhere on the board
/L Band/SPI1_CS: U1.A4 (XDMA_EVENT_INTR0); also elsewhere on the board
/L Band/SPI1_MISO: U1.C12 (UART0_CTSN); also elsewhere on the board
/L Band/SPI1_MOSI: U1.C13 (UART0_RTSN); also elsewhere on the board
/L Band/SPI1_SCLK: U1.C5 (ECAP0_IN_PWM0_OUT); also elsewhere on the board
/OPD and I2C Peripherals/I2C2_SYS_DISABLE: U1.R6 (GPMC_AD13); also elsewhere on the board
/OPD and I2C Peripherals/I2C2_SYS_SCL: U1.A10 (UART1_RTSN); also elsewhere on the board
/OPD and I2C Peripherals/I2C2_SYS_SDA: U1.B10 (UART1_CTSN); also elsewhere on the board
/OPD and I2C Peripherals/OPD_nENABLE: U1.C3 (MCASP0_AXR1); also elsewhere on the board
/OPD and I2C Peripherals/OPD_nFAULT: U1.B3 (MCASP0_FSR); also elsewhere on the board
/OSD3358: SIP C/CAN1_RXD: U1.B11 (UART1_TXD), U8.4 (RXD)
/OSD3358: SIP C/CAN1_TXD: U1.A11 (UART1_RXD), U8.1 (TXD)
/OSD3358: SIP C/EMMC_CMD: R70.2 (22), U1.P1 (GPMC_CSN2), U9.M5 (CMD)
/OSD3358: SIP C/EMMC_D0: R70.6 (66), U1.R3 (GPMC_AD0), U9.A3 (D0)
/OSD3358: SIP C/EMMC_D1: R71.1 (11), U1.R2 (GPMC_AD1), U9.A4 (D1)
/OSD3358: SIP C/EMMC_D2: R71.9 (99), U1.R1 (GPMC_AD2), U9.A5 (D2)
/OSD3358: SIP C/EMMC_D3: R70.7 (77), U1.T3 (GPMC_AD3), U9.B2 (D3)
/OSD3358: SIP C/EMMC_D4: R70.4 (44), U1.T2 (GPMC_AD4), U9.B3 (D4)
/OSD3358: SIP C/EMMC_D5: R70.3 (33), U1.T1 (GPMC_AD5), U9.B4 (D5)
/OSD3358: SIP C/EMMC_D6: R71.8 (88), U1.P4 (GPMC_AD6), U9.B5 (D6)
/OSD3358: SIP C/EMMC_D7: R71.2 (22), U1.R4 (GPMC_AD7), U9.B6 (D7)
/OSD3358: SIP C/EMMC_SCK: R70.8 (88), U1.P2 (GPMC_CSN1), U9.M6 (SCK)
/OSD3358: SIP C/EMMC_nRST: R71.3 (33), U1.R13 (GPMC_A4), U9.K5 (~RST)
/OSD3358: SIP C/L_BAND_ENABLE: U1.T13 (GPMC_A3); also elsewhere on the board
/OSD3358: SIP C/MMC1_CD: J5.CD (CD#), R69.6 (66), U1.C14 (SPI0_CS1)
/OSD3358: SIP C/MMC1_CLK: J5.5 (CLK), R69.3 (33), U1.B15 (MMC0_CLK)
/OSD3358: SIP C/MMC1_CMD: J5.3 (CMD/DI), R69.8 (88), U1.B16 (MMC0_CMD)
/OSD3358: SIP C/MMC1_DAT0: J5.7 (DAT0/DO), R69.9 (99), U1.A16 (MMC0_DAT0)
/OSD3358: SIP C/MMC1_DAT1: J5.8 (DAT1), R69.4 (44), U1.A15 (MMC0_DAT1)
/OSD3358: SIP C/MMC1_DAT2: J5.1 (DAT2), R69.7 (77), U1.C16 (MMC0_DAT2)
/OSD3358: SIP C/MMC1_DAT3: J5.2 (DAT3/CS), R69.2 (22), U1.C15 (MMC0_DAT3)
/OSD3358: SIP C/PIN7-GPIO: R30.2, U1.B2 (MCASP0_AXR0), U42.3
/OSD3358: SIP C/PIN8-GPIO: R90.2, U1.A1 (MCASP0_ACLKX), U42.1
/OSD3358: SIP C/RADIO_nFLT: U1.A3 (MCASP0_ACLKR); also elsewhere on the board
/OSD3358: SIP C/SPI0_CS: U1.A14 (SPI0_CS0); also elsewhere on the board
/OSD3358: SIP C/SPI0_MISO: U1.B13 (SPI0_D0); also elsewhere on the board
/OSD3358: SIP C/SPI0_MOSI: U1.B14 (SPI0_D1); also elsewhere on the board
/OSD3358: SIP C/SPI0_SCLK: U1.A13 (SPI0_SCLK); also elsewhere on the board
/OSD3358: SIP C/UHF_ENABLE: U1.T12 (GPMC_A0); also elsewhere on the board
/OSD3358: SIP C/UHF_IRQ: U1.P15 (GPMC_WAIT0); also elsewhere on the board
/OSD3358: SIP C/UHF_PA_ENABLE: U1.T16 (GPMC_A11); also elsewhere on the board
/OSD3358: SIP C/UHF_TOT_CLEAR: U1.R15 (GPMC_A10); also elsewhere on the board
/OSD3358: SIP C/UHF_TOT_OK: U1.T15 (GPMC_A9); also elsewhere on the board
/OSD3358: SIP C/USR1: R42.1, U1.P13 (GPMC_A5)
/OSD3358: SIP C/USR2: R43.1, U1.T14 (GPMC_A6)
/OSD3358: SIP C/USR3: R44.1, U1.R14 (GPMC_A7)
/OSD3358: SIP C/USR4: R45.1, U1.P14 (GPMC_A8)
/PIN7-OUT: R94.1; also elsewhere on the board
/PIN8-OUT: R91.1; also elsewhere on the board
GND: C16.2, C17.2, C18.2, C19.2, C20.2, C21.2, C22.2, C23.2, C24.2, C25.2, C48.1, D4.1 (K), D5.1 (K), D6.1 (K), D7.1 (K), J5.6 (VSS), J5.CGND1 (CGND), J5.CGND2 (CGND), J5.CGND3 (CGND), J5.CGND4 (CGND), J5.CGND5 (CGND), J5.CGND6 (CGND), J5.GND (VSS), R30.1, R90.1, U8.2 (GND), U9.A6 (VSSIO), U9.C4 (VSSQ), U9.E7 (VSSIO), U9.G5 (VSSIO), U9.H10 (VSSIO), U9.J5 (VSSIO), U9.K8 (VSSIO), U9.N2 (VSSQ), U9.N5 (VSSQ), U9.P4 (VSSQ), U9.P6 (VSSQ), U42.2 (GND); also elsewhere on the board
unnamed: D4.2 (A), R42.2
unnamed: D5.2 (A), R43.2
unnamed: D6.2 (A), R44.2
unnamed: D7.2 (A), R45.2
unnamed: R91.2, U42.6
unnamed: R94.2, U42.4
unnamed: TP38.1 (1_1), U1.R12 (GPMC_A1)
unnamed: TP39.1 (1_1), U1.P12 (GPMC_A2)
unnamed: TP170.1 (1_1), U1.T4 (GPMC_AD8)
unnamed: TP162.1 (1_1), U1.P5 (GPMC_AD9)
unnamed: TP126.1 (1_1), U1.R5 (GPMC_AD10)
unnamed: TP124.1 (1_1), U1.T5 (GPMC_AD11)
unnamed: TP89.1 (1_1), U1.P6 (GPMC_AD12)
unnamed: TP42.1 (1_1), U1.T6 (GPMC_AD14)
unnamed: TP46.1 (1_1), U1.P7 (GPMC_AD15)
unnamed: TP64.1 (1_1), U1.N3 (GPMC_BEN0_CLE)
unnamed: TP68.1 (1_1), U1.T7 (GPMC_CLK)
unnamed: TP47.1 (1_1), U1.P3 (GPMC_CSN0)
unnamed: TP48.1 (1_1), U1.R7 (GPMC_CSN3)
unnamed: TP66.1 (1_1), U1.N1 (GPMC_OEN_REN)
unnamed: TP65.1 (1_1), U1.N2 (GPMC_WEN)
unnamed: TP33.1 (1_1), U1.B1 (MCASP0_AHCLKR)
unnamed: TP34.1 (1_1), U1.C4 (MCASP0_AHCLKX)
unnamed: TP27.1 (1_1), U1.A2 (MCASP0_FSX)
unnamed: TP35.1 (1_1), U1.B4 (XDMA_EVENT_INTR1)
unnamed: C19.1, C20.1, U9.C2 (VDDI)

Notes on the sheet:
0805
TO L BAND RADIO
eMMC Flash Memory
GPIO to the backplane for controlling various peripherals (e.g., ESI's S Band Radio) on pins SPARE7 and SPARE8.
Removable uSD Card
Need ~2.2uF, using two 1uF for simplicity
TO L RADIO
SIP pin states ("ZZ", "LL", "ZL", etc) are GPIO states of the pin during and immediately after a reset. See Pg 18-47 in https://www.ti.com/lit/ds/symlink/am3358.pdf
USR LEDs
Z[L|0|CLK]
TO C3 I2C Peripherals
16 GB (128 Gb) eMMC
(Clear this area on schematic sheet for eMMC unconnected pin array)
All resistors are 0603 1% AEC-Q200 unless marked. All capacitors are 0603 AEC-Q200 Vw >= 16V X5R or better unless marked.
CAN Transceiver
TO UHF RADIO

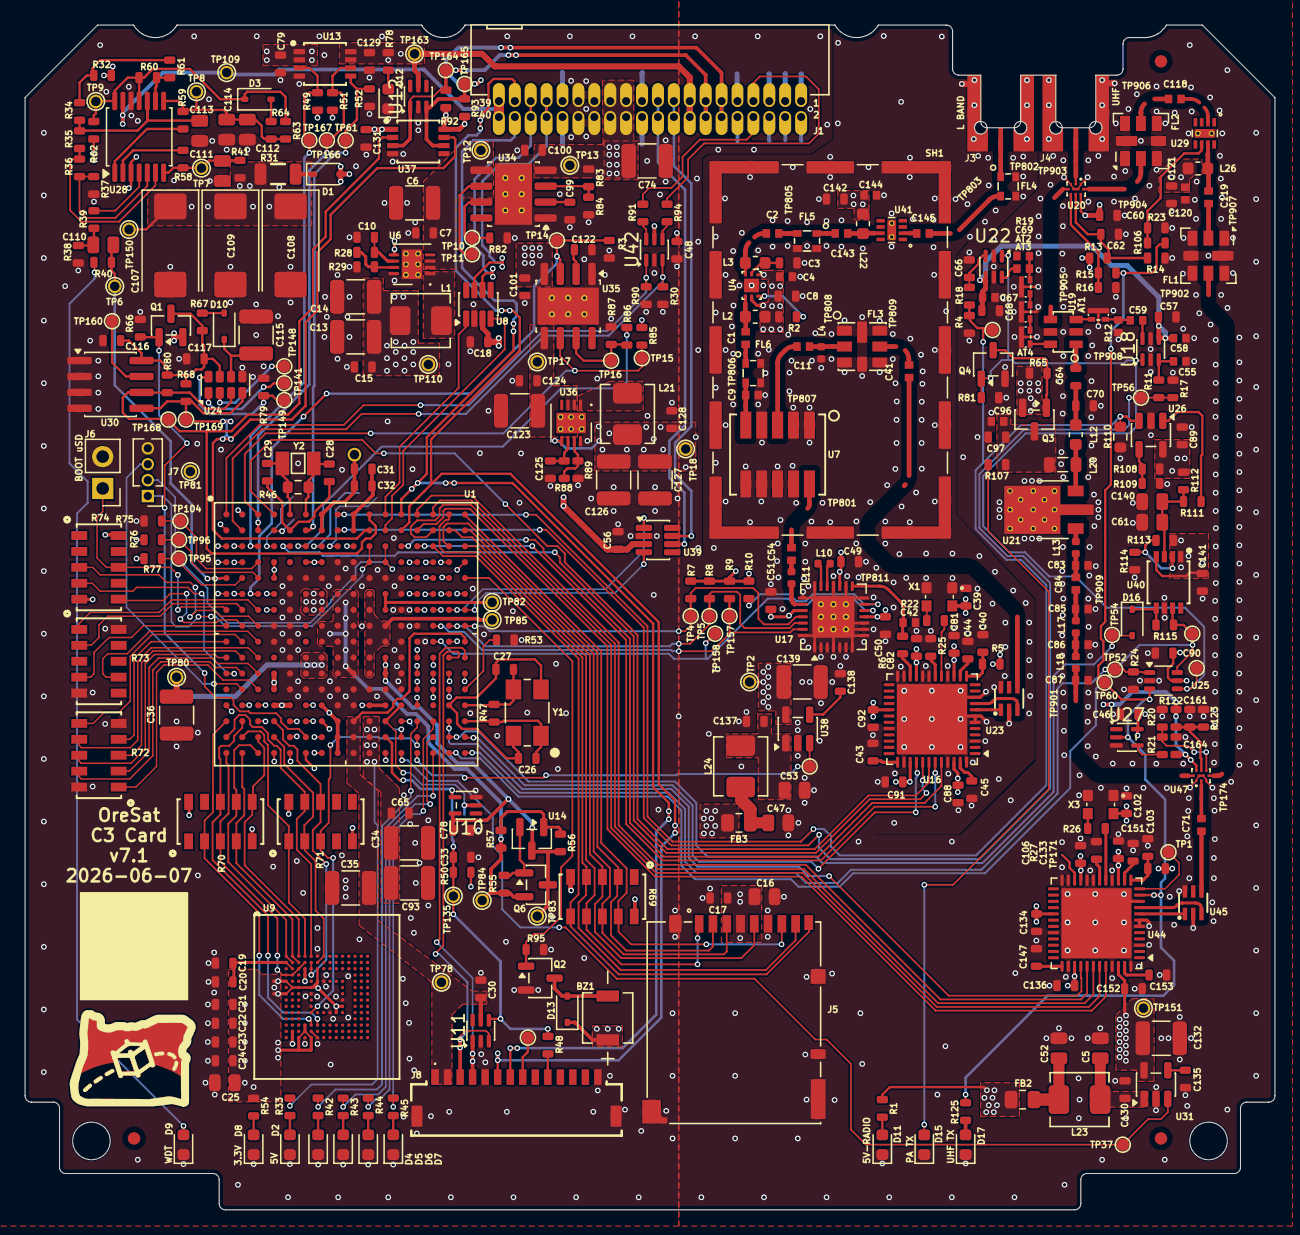
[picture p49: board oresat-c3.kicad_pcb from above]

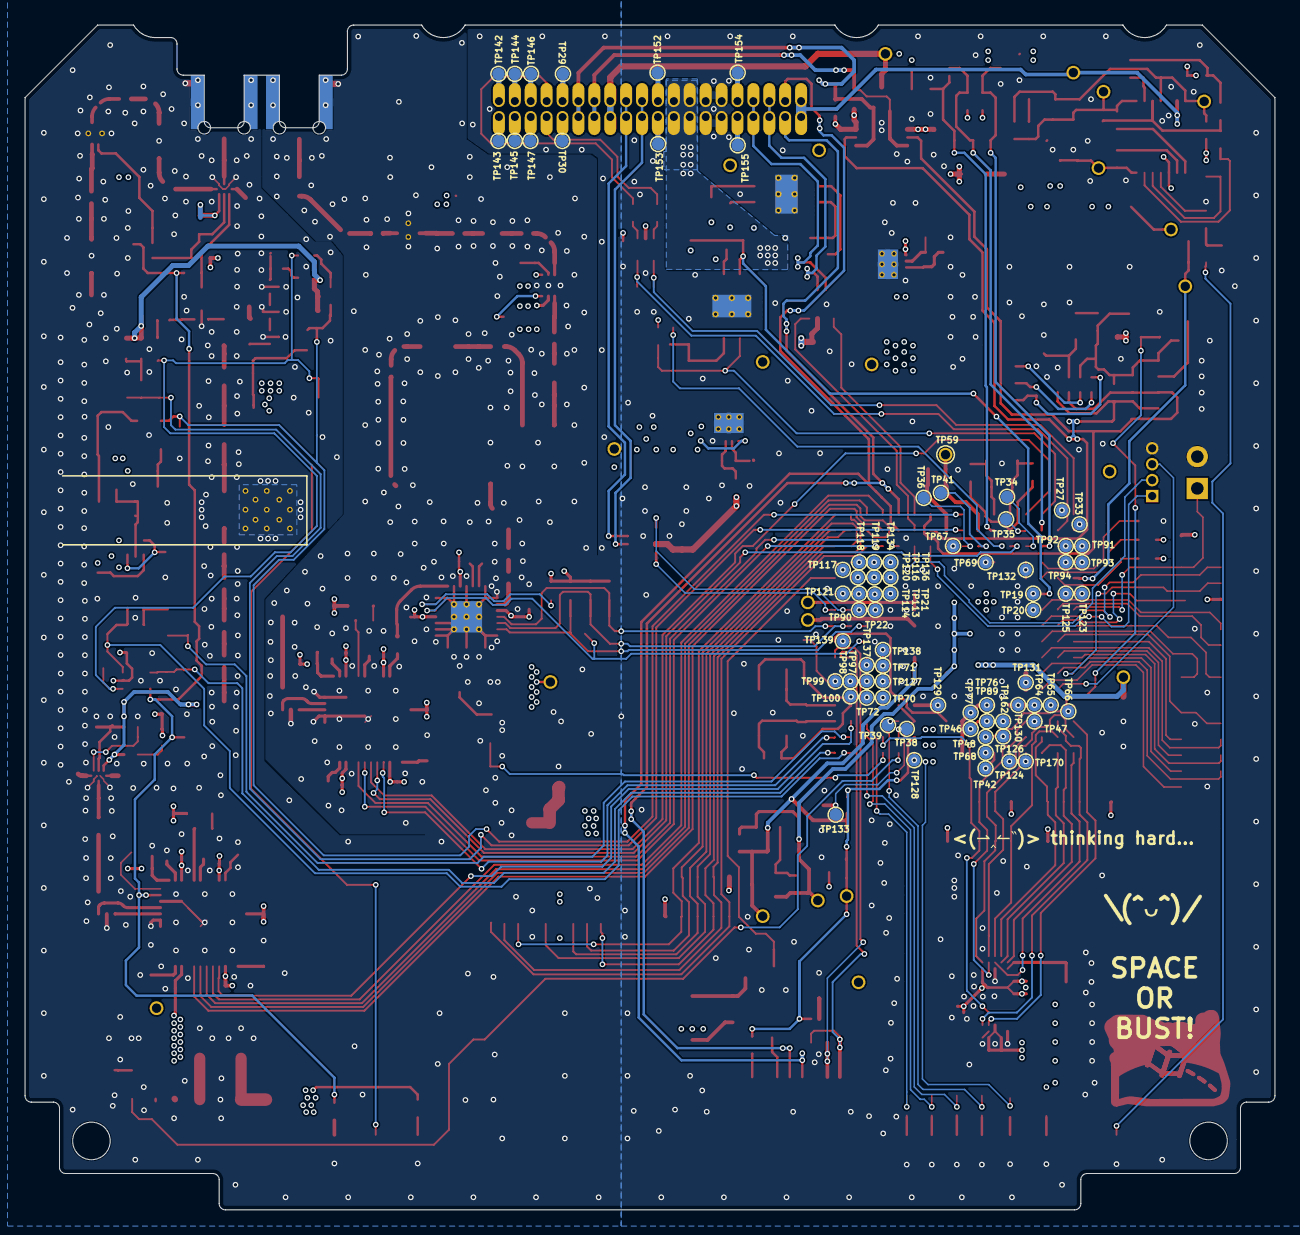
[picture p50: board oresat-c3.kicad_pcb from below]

Board: 4 copper layers, 99.8 x 94.6 mm, 504 parts (76 on the bottom side), 342 nets.

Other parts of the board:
LOGO: logo-small

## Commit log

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2019-06-26 Updated to the latest card outline. Updated OreSat main connector pinout. Got rid of some junk we don't need for C3.
    [c3-card.brd, c3-card.sch]
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2019-11-12 Added the circuit breaker schematic and wired it to the board part tps25961
    [oresat-c3-prototype.brd, oresat-c3-prototype.sch]
2019-11-12 I corrected R_ILIM on the CB to set the over current limit to 0.302 A.
    [oresat-c3-prototype.brd, oresat-c3-prototype.sch]
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2019-11-14 Fixed a couple other error check items
    [oresat-c3-prototype.brd, oresat-c3-prototype.sch]
2019-11-15 Fixed VBUSP routing around the SPS
    [oresat-c3-prototype.brd]
2019-11-16 Switched the MAX892 in for the OPD circuit breaker and rerouted the wires
    [oresat-c3-prototype.brd, oresat-c3-prototype.sch]
2019-11-17 Added the Radio breakout board schematic and layout to the eagle folder under DVK2C-breakout.sch
    [DVK2C-breakout.brd, DVK2C-breakout.sch]
2019-11-17 Added 2 radio headers and associated test points to sheet 1. Components need to be placed and nets named appropriately
    [oresat-c3-prototype.brd, oresat-c3-prototype.sch]
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2019-11-19 Fixed OPD I2C Pullups to OPD_PWR
    [oresat-c3-prototype.brd, oresat-c3-prototype.sch]
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2019-11-21 fixed angles on jtag traces and added an WDT diode
    [oresat-c3-prototype.brd, oresat-c3-prototype.sch]
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2019-11-21 Fixed some erc errors
    [oresat-c3-prototype.brd, oresat-c3-prototype.sch]
2019-11-21 Fixed some DRC errors
    [oresat-c3-prototype.brd]
2019-11-21 fixed all drc and erc errors, some warnings remain
    [oresat-c3-prototype.brd]
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2019-11-21 Fixed some additional stubs and air wires
    [oresat-c3-prototype.brd]
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2019-11-24 Polishing by mysterious outside forces. Schematic cleanup, including removing some unecessary components, moved radios and MMC carrier to actually fit on the card, moved power around to be more optim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
    [oresat-c3-prototype.brd, oresat-c3-prototype.sch]
2019-11-24 Fix VCAP, fix JTAG header, remove weird 0.1in headers which make SPI bus go everywhere, fix component tyes, add test points, polish.
    [oresat-c3-prototype.brd, oresat-c3-prototype.sch]
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2019-11-25 Replaced new ICs with versions in the oresat-eagle-libraries repo
    [C3-Practicum.xlsx, oresat-c3-prototype-raw.csv, oresat-c3-prototype.brd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]
2019-11-25 replaced the SD Card socket with a part in the oresat libraries
    [oresat-c3-prototype.brd, oresat-c3-prototype.sch]
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2019-11-26 Corrected part counts in the BOM
    [C3-Practicum.xlsx]
2019-11-26 Added the SD card socket and changed vendors for the MAX892 on the BOM
    [C3-Practicum.xlsx]
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2020-01-21 Make changes to oresat-c3-v1 board
    Fix eMMC pin out to better match datasheet
    Route data lines to match lengths
    [oresat-c3-v1.brd, oresat-c3-v1.sch]
2020-01-21 Ran an initial ERC DRC on the v1 board, cleared some errors and left the rest for a board review
    [oresat-c3-v1.brd, oresat-c3-v1.sch]
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2020-01-22 Cleared errors for eMMC Added documentation for eMMC
    [oresat-c3-v1.brd, oresat-c3-v1.sch]
2020-01-22 Replaced eMMC package from generic to one for C3 board specific
    [Backup.oresat-c3-v1.brd, Backup.oresat-c3-v1.sch]
2020-01-23 C3 Functional Description Folder
    Contains images of all block diagrams and a document that describes the functionality of each subsystem on the C3 board.
    [oresat-c3-prototype.brd, oresat-c3-prototype.sch]
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2020-01-24 Made Design review changes to C3 board
    updated changes made in design review doc
    [oresat-c3-v1.brd, oresat-c3-v1.sch]
2020-01-24 Fix net error
    [oresat-c3-v1.brd, oresat-c3-v1.sch]
2020-01-24 Replace lost wire
    [oresat-c3-v1.brd]
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2020-01-25 Fix some connections
    [oresat-c3-v1.brd, oresat-c3-v1.sch]
2020-01-25 Cleared all ERC and DRC
    Made design changes as per design review
    [oresat-c3-v1.brd, oresat-c3-v1.sch]
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2020-01-25 final stamp, minor schematic clean up and error checking
    [oresat-c3-v1.brd, oresat-c3-v1.sch]
2020-01-29 switched the TX and RX pins to be the correct way
    [oresat-c3-v1_WRONG_FTDI.brd, oresat-c3-v1_WRONG_FTDI.sch]
2020-01-31 A wee bit of polish to get it off to OSH Park. v1 sent to fab.
    [c3-card.brd, c3-card.sch, oresat-c3-v1.brd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]
2020-01-31 Removed WRONG files.
    [oresat-c3-v1_WRONG_FTDI.brd, oresat-c3-v1_WRONG_FTDI.sch]
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2020-02-05 Replaced non 0603 passive components with available 0603 equivalents
    [oresat-c3-v2.brd, oresat-c3-v2.sch]
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2020-02-07 Removed Jumpers and moved eMMC, processor, and more
    Mostly reconnected , made changed to some of the polygons
    [oresat-c3-v2.brd, oresat-c3-v2.sch]
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2020-02-19 Wired in the edge connector and added the data sheet for the littlefuse TVS diode
    [oresat-c3.brd, oresat-c3.sch]
2020-02-20 Removed jumper Fixed DRC errors
    [oresat-c3.brd, oresat-c3.sch]
2020-02-21 Updated Eagle Brd/Schematic
    Add Supervisory IC onto the C3 brd and schematic. Only implemented the watchdog timer functionality. The pins that are used to detect for brown out conditions have been left floating until further discussed.
    [oresat-c3.brd, oresat-c3.sch]
2020-02-21 Minor adjustments
    Minor adjustments to edge connector and labeling, shifted some of the Watchdog circuit
    [oresat-c3.brd, oresat-c3.sch]
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2020-02-29 put in segregated ground planes, added the version of the project proposal that was signed to the docs folder
    [oresat-c3.brd, oresat-c3.sch, transceiver-AX5043-v1.brd]
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2020-03-04 Spelling fix
    [oresat-c3.sch]
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2020-03-07 Added the L band Local oscillator
    [mixer-MAC-24+.brd, mixer-MAC-24+.sch, oresat-c3.brd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]
2020-03-07 Modified some L band design blocks and in corporated them into the C3
    [oresat-c3.brd, oresat-c3.sch]
2020-03-07 Allocated MCU pins for deployment system, sythnesizer control, and feedback. Added initial deployment circuitry.
    [oresat-c3.brd, oresat-c3.sch]
2020-03-07 Added in UHF power tree design block
    removed the backup eagle files the # ones
    [oresat-c3.brd, oresat-c3.sch]
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2020-03-09 Edit WDT Symbol and Removed TVS on SD line
    Moved WDI onto left side of WDT symbol. Removed U8 (TVS Diodes connected to SD line)
    [oresat-c3.brd, oresat-c3.sch]
2020-03-13 Made some of Revision changes
    Delete everything on the reference layer.
    Uniform ground planes on all layers.
    Move opd and uhf power to power sheet
    [oresat-c3.brd, oresat-c3.sch]
2020-03-14 Made more revision changes and making room to replace the MCU
    [oresat-c3.brd, oresat-c3.sch]
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2020-03-16 completed making room for new MCU
    Made many design review changes
    removed all temp save files
    [oresat-c3.brd, oresat-c3.sch]
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2020-03-17 swapped the L-band and UHF areas
    [oresat-c3.brd, oresat-c3.sch]
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2020-03-20 Replaced parts form tova library with their own library components
    [oresat-c3.brd, oresat-c3.sch]
2020-03-22 Fixed L band Schematic and layout after move to the center of the C3 card
    [oresat-c3.brd, oresat-c3.sch]
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2020-03-22 Fixed U17
    [oresat-c3.brd, oresat-c3.sch]
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2020-03-23 Some ERC and DRC fixes not all
    [oresat-c3.brd, oresat-c3.sch]
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2020-03-25 DRC clean up , Fixed small Test Points
    [oresat-c3.brd, oresat-c3.sch]
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2020-03-26 Fixed some air wires
    [oresat-c3.brd, oresat-c3.sch]
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2020-03-26 Fixed more Airwires
    [oresat-c3.brd, oresat-c3.sch]
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2020-03-30 Fixed some DRC errors (airwires, dimention, etc)
    [oresat-c3.brd, oresat-c3.sch]
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2020-04-10 Fixed Airwires; wire stubs Approved warnings
    [oresat-c3.brd, oresat-c3.sch]
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2020-04-16 v2 OFF TO FABgit status Lots of cleanup on TNAMEs, cleanup on solder mask openings for microstrips, a bit of power rework near AX5043s. TODO: Make all 0603 components the smaller C version, which can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
    [oresat-c3.brd, oresat-c3.sch]
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2020-04-28 Fix board Schematic error
    [oresat-c3.brd, oresat-c3.sch]
2020-04-29 Fixing Attributes
    [oresat-c3.brd, oresat-c3.sch]
2020-04-29 Fix Sync Error
    [oresat-c3.brd, oresat-c3.sch]
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2020-06-25 Added GPIO to antenna deploy circuits, replaced all 0603 cap footprints
    [oresat-c3.brd, oresat-c3.sch]
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2020-06-28 Shifted component for clearance, change 16Mhz crystal, added 32.768kHz
    Added synthesizer programming jumpers, clean up tname, found smaller diodes for D7
    [oresat-c3.brd, oresat-c3.sch]
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2020-06-29 Minor Text fixes
    [oresat-c3.brd]
2020-07-20 Tried to fix EAGLE errors for OSH Park; failed, we need to make Gerbers for them.
    [oresat-c3.brd]
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2020-08-18 Added PA design block , Replaced u Processor, Fixed/replaced X1 crystal
    [oresat-c3.brd, oresat-c3.sch]
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2020-12-13 Mid-work commit for review. Cleaned up some of the more trivial issues, and have the UHF about 50% laid out. Moved PA closer to side wall for better thermals, compacted whole layout.
    [oresat-c3.brd, oresat-c3.sch]
2020-12-13 Fixed weird invalid polygon issue with only 1 vertex ... EAGLE, stop it.
    [oresat-c3.brd]
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2020-12-29 Added mdwn file on RF microstrips, more layout on board, fixed layer 16 to side wall for the PA, fixed a bunch of github isusues.
    [oresat-c3.brd, oresat-c3.sch]
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2021-01-03 Swapped diodes out with the ones we found for the battery pack. Moved some text around. Ran ERC and DRC again.
    [oresat-c3.brd, oresat-c3.sch]
2021-01-03 Added FRAM, because FRAMgit add oresat-c3.brd oresat-c3.sch, added 5th order LPF for UHF TX. Waiting on final values of LPF and time out timer (TOT) from Glenn, then need to fix attributes and ship!
    [oresat-c3.brd, oresat-c3.sch]
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2021-01-04 Fixed up PA TSTOP and TCREAM, fixed quad nchannel TCREAM, added call signs of main C3 folks, fixed 2mm miter on RF lines.
    [oresat-c3.brd, oresat-c3.sch]
2021-01-31 Updated date BOM for C3 V4, fixed some parts for future V5.
    [oresat-c3-BOM.xlsx, oresat-c3.brd, oresat-c3.sch]
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2021-02-07 Changes to the timeout timer based on available parts; updated SCH and BOM. Also fixed off-by-one-row errors for Mouser parts.
    [oresat-c3-BOM.xlsx, oresat-c3.brd, oresat-c3.sch]
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2021-02-14 Added pulldowns to M4_PA_ENABLE and TOT_OUT to prevent accidental turn on of the PA. Fixed TOT pin swap of !LATCH and !SHDN. Moved eMMC pull-up resistors to EMMC_VDD so that when the eMMC is powered 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
    [oresat-c3.brd, oresat-c3.sch]
2021-02-14 Fixed swap of pins 2 and 3 on the TOT; renamed TOT pins to be better names (TOT_OUT is now !TOT_PA_DISABLE).
    [oresat-c3.brd, oresat-c3.sch]
2021-02-14 Oh, and yeah, layout for the TOT fix. Also caught a TOT_OUT outlier.
    [oresat-c3.brd, oresat-c3.sch]
2021-02-16 Fixed some DRC issues.
    [oresat-c3.brd]
2021-02-22 Fixed 32 KHz crystal value.
    [oresat-c3.brd, oresat-c3.sch]
2021-03-06 Package cleanup: move away from samacsys parts which are now mostly wrong. Move to all -C-NO-SILK parts for 0402 and 0603. Change K to k for resistors.
    [oresat-c3.brd, oresat-c3.sch]
2021-03-08 Updated TOT values to make it 1 second long. Added "RF test points" and some associated ground points with level values to help future debugging.
    UGH: in previous commit, forgot to mention the most important fixes:
    - Fixed TOT swap of pin 2,3 and the non-working functionality of the !SHDN. M4 now unlatches output only, and does not affect output of the circuit.
    - Fixed WDT with latest "Tim" version (thanks Tim!) with small changes to values to operate correctly.
    [oresat-c3.brd, oresat-c3.sch]
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2021-03-08 Minor polishing with Glenn, removed L band TX components, fixed BOM.
    [oresat-c3-BOM.xlsx, oresat-c3.brd, oresat-c3.sch]
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2022-12-29 Removed GPS splitter and fixed RF path.
    [oresat-c3.brd, oresat-c3.sch]
2022-12-30 Fixes issues #47, #44, #43, #36 - all the RF issues around the missing emitter degeneration.
    [oresat-c3.brd, oresat-c3.sch]
2022-12-30 Fixes #39 - added ILIM to ADC on PA3 via 10K resistor.
    [oresat-c3.brd, oresat-c3.sch]
2022-12-30 Fixes #41: change thermistor on UHF PA to 0603
    [oresat-c3.brd, oresat-c3.sch]
2022-12-30 Fixes #40 - more capacitance on 3.3V SPS in and out to help with brownouts.
    [oresat-c3.brd, oresat-c3.sch]
2023-02-19 Fixes some test point numbers.
    [oresat-c3.brd, oresat-c3.sch]
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2023-05-03 Added watchdog and I2C sheets; fixed library paths and library references. Started on watchdog schematic.
    [oresat-c3-sch-i2c-peripherals.kicad_sch, oresat-c3-sch-watchdog.kicad_sch, oresat-c3.kicad_sch]
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2023-05-05 Simulated 30 second v6 watchdog circuit and fixed up watchdog in KiCAD.
    [oresat-c3-sch-watchdog.kicad_sch]
2023-05-21 Added more to UHF schematic, fixed github issues 54 and 53
    [oresat-c3-sch-uhf-band.kicad_sch]
2023-05-30 C3 v6 schematic now 80% done. OSD2258 IC has been gone over with a fine tooth comb and simplified as much as possible. OSD3358 pinout compared to RED board and PocketBeagle. What's left: lots of litt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
    [oresat-c3-sch-connectors.kicad_sch, oresat-c3-sch-deployers.kicad_sch, oresat-c3-sch-l-band.kicad_sch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]
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2023-06-01 Flipped UHF schematic to be L to R, more polish, added direction arrows. Started on L band radio. Added latest oresat-kicad libraries, started to remove old libraries (e.g., GPS).
    [oresat-c3-sch-deployers.kicad_sch, oresat-c3-sch-l-band.kicad_sch, oresat-c3-sch-opd-and-i2c.kicad_sch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]
2023-06-01 Rough draft schematic of C3 v6 done. L band fixed, some GPIO attached, awaiting design review before final attachments.
    [oresat-c3-sch-deployers.kicad_sch, oresat-c3-sch-l-band.kicad_sch, oresat-c3-sch-opd-and-i2c.kicad_sch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]
2023-06-02 First round of ERC fixes.
    [oresat-c3-sch-connectors.kicad_sch, oresat-c3-sch-deployers.kicad_sch, oresat-c3-sch-l-band.kicad_sch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]
2023-06-02 Sane amount of ERC errors now; mostly library cleanups.
    [oresat-c3-sch-connectors.kicad_sch, oresat-c3-sch-deployers.kicad_sch, oresat-c3-sch-i2c-peripherals.kicad_sch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]
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2023-06-03 Try harder with sheet 1 footprints. Import sheet 1 footprints over, and then fix all the things on sheet 1 that break. New card better card outline, all connectors roughly placed.
    [oresat-c3-sch-connectors.kicad_sch, oresat-c3-sch-deployers.kicad_sch, oresat-c3-sch-opd-and-i2c.kicad_sch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]
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2023-06-08 Big C3 cleanup with Glenn; radios off of one SPS + separate LDOs, removed lots of test 0 ohm resistors, cleaned up capacitance, and finally wired everything up to the octavo. ZERO ERC errors.
    [oresat-c3-sch-connectors.kicad_sch, oresat-c3-sch-deployers.kicad_sch, oresat-c3-sch-l-band.kicad_sch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]
2023-06-08 Updated test points, fixed some more hidden ERCs.
    [oresat-c3-sch-deployers.kicad_sch, oresat-c3-sch-l-band.kicad_sch, oresat-c3-sch-opd-and-i2c.kicad_sch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]
2023-06-10 Fixed test points; added RF test points. Started on layout and component packages for UHF radio.
    [oresat-c3-sch-connectors.kicad_sch, oresat-c3-sch-deployers.kicad_sch, oresat-c3-sch-l-band.kicad_sch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]
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2023-06-22 Fixed footprints and laid out WDT and OPD circuitry.
    [oresat-c3-sch-connectors.kicad_sch, oresat-c3-sch-deployers.kicad_sch, oresat-c3-sch-l-band.kicad_sch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]
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2023-06-27 Rough draft layout of UHF radio. Fixed duplicated test points.
    [oresat-c3-sch-deployers.kicad_sch, oresat-c3-sch-opd-and-i2c.kicad_sch, oresat-c3-sch-osd3358-usb-xtal.kicad_sch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]
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2023-06-29 Added reset states of GPIO lines to OSD3358 pins in schematic so we know what pulls up unexpectedly. Re-arranged a few pins that should not pull up on boot.
    [oresat-c3-sch-osd3358-power.kicad_sch, oresat-c3-sch-osd3358-sd-emmc.kicad_sch, oresat-c3-sch-osd3358-sysboot.kicad_sch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]
2023-07-05 An evening of cleanups from the design review. Includes lots of ERC and DRC cleanup, although still over 450 DRC errors mostly from RF keepouts. Fixed PA ground connection, notes on pin reset configu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
    [oresat-c3-sch-connectors.kicad_sch, oresat-c3-sch-l-band.kicad_sch, oresat-c3-sch-opd-and-i2c.kicad_sch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]
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2023-07-11 Last of the ERC and DRC errors! only polishing left.
    [oresat-c3-sch-l-band.kicad_sch, oresat-c3-sch-osd3358-power.kicad_sch, oresat-c3-sch-osd3358-sd-emmc.kicad_sch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]
2023-08-24 More polish; fixed all non-RF DRCs.
    [oresat-c3-sch-connectors.kicad_sch, oresat-c3-sch-l-band.kicad_sch, oresat-c3-sch-osd3358-sd-emmc.kicad_sch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]
2023-08-27 More fixes. TOT_CLEAR moved to a non HH pin, cleaned up in2 zones, moved fiducials, set dv/dt on power switches, added HW ID (5 bits) rechecked ADC 1.8V limits and fixed resistor values to match.
    [oresat-c3-sch-deployers.kicad_sch, oresat-c3-sch-osd3358-sd-emmc.kicad_sch, oresat-c3-sch-osd3358-sysboot.kicad_sch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]
2023-08-27 Updated AX5043 foot print, moved synthesize to correct L length, fixed more grounds
    [oresat-c3-sch-l-band.kicad_sch, oresat-c3-sch-osd3358-sd-emmc.kicad_sch, oresat-c3-sch-osd3358-usb-xtal.kicad_sch]
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2023-08-28 Cleaned up RF routing. Stitched (automatically). RF routing cleanup. Marked 0402s and replacedsome 0603 with 0402. Silkscreen cleanup. Just BOM optimization and purchasing left.
    [oresat-c3-sch-l-band.kicad_sch, oresat-c3-sch-osd3358-sd-emmc.kicad_sch, oresat-c3-sch-uhf-band.kicad_sch]
2023-08-28 First round of BOM fixes and optimizations.
    [oresat-c3-sch-deployers.kicad_sch, oresat-c3-sch-opd-and-i2c.kicad_sch, oresat-c3-sch-osd3358-sd-emmc.kicad_sch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]
2023-08-28 Cleanup of crystals, more BOM reduction and fixes.
    [oresat-c3-sch-opd-and-i2c.kicad_sch, oresat-c3-sch-osd3358-sd-emmc.kicad_sch, oresat-c3-sch-osd3358-usb-xtal.kicad_sch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]
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2023-09-04 Fixed part name, removed solder mask from the back of some of the library components for venting.
    [oresat-c3-sch-osd3358-power.kicad_sch, oresat-c3-sch-osd3358-sd-emmc.kicad_sch]
2023-09-11 More changes to 6.1: fix UVLO on TPS, fix uSD card datasheet link, fix MMC number for SD card
    [oresat-c3-sch-osd3358-sd-emmc.kicad_sch, oresat-c3-sch-power.kicad_sch]
2023-09-15 Fixed R82 so that the damn thing doesn't reboot every two seconds. Fixed R63 to extend the watchdog timer. Fixed R83 and R84 in order to set the UVLO correctly.
    [oresat-c3-sch-osd3358-sd-emmc.kicad_sch, oresat-c3-sch-power.kicad_sch, oresat-c3-sch-watchdog.kicad_sch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]
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2023-12-21 Fixed some issues, including adding mrore capacitance. Also switched back to 0.38 mm for 50 ohm lines.
    [oresat-c3-sch-osd3358-power.kicad_sch, oresat-c3-sch-power.kicad_sch, oresat-c3-sch-uhf-band.kicad_sch]
2023-12-21 Fixed test points and debugging info on AX5043s with Theo
    [oresat-c3-sch-uhf-band.kicad_sch]
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2024-03-18 Fixed Q1 in the I2C subsystem, which was backward but we never noticed. Removed hardware ID resistors and added back in test points, since HW ID is now stored in internal EEPROM. Updated power measur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
    [oresat-c3-sch-connectors.kicad_sch, oresat-c3-sch-deployers.kicad_sch, oresat-c3-sch-l-band.kicad_sch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]
2024-03-18 Fixed accidental deletion error in schematic on eMMC net, updated symbols and packages to match library, updated date on silk screen, and pushed UHF power supply out of the way of the frame boss so i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
    [oresat-c3-sch-opd-and-i2c.kicad_sch, oresat-c3-sch-osd3358-sd-emmc.kicad_sch, oresat-c3-sch-osd3358-usb-xtal.kicad_sch]
2024-04-01 Last changes to 6.1 after design review today.
    Added logo.
    Brought up to KiCAD 8.0.1.
    Added text next to smpm connectors.
    Fixed some 0.127 traces that didn't need to be that thin on nRESET.
    Fix silkscreen refdeses on new components.
    Move pin 1 marker on the BP0805A1308.
    Remove thermals on PA bottom layer.
    Added oresat-c3-eagle-import symbols and footprints so everything is local.
    [oresat-c3-sch-connectors.kicad_sch, oresat-c3-sch-deployers.kicad_sch, oresat-c3-sch-l-band.kicad_sch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]
2024-04-01 OOof, almost ordered with incorrect RF netclass. Reset to 0.5 mm keepouts.
2024-04-09 BOM cleanups; modified test points to not show up on BOMs, fixed some minor BOM shenaigans (3k vs 3.0k), and imported into the board.
    [oresat-c3-sch-connectors.kicad_sch, oresat-c3-sch-deployers.kicad_sch, oresat-c3-sch-l-band.kicad_sch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]
2024-04-10 Fixed more part numbers while in process of doing BOM inventory, including eMMC and FRAM.
    [oresat-c3-sch-opd-and-i2c.kicad_sch, oresat-c3-sch-osd3358-power.kicad_sch, oresat-c3-sch-osd3358-sd-emmc.kicad_sch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]
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2025-12-28 C3 v6.1 release
    Updated to KiCad 9.0.6. Updated to version 6.1; there are small changes that have been lost in time. Lots of new ERC and DRC errors that need to be cleaned up.
    [oresat-c3-sch-connectors.kicad_sch, oresat-c3-sch-deployers.kicad_sch, oresat-c3-sch-l-band.kicad_sch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]
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2026-01-24 started at86 replacement, work in progress
    [oresat-c3-sch-connectors.kicad_sch, oresat-c3-sch-deployers.kicad_sch, oresat-c3-sch-l-band.kicad_sch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]
2026-02-02 Replaced AX5043 for UHF and added TX/RX switch control
    [oresat-c3-sch-uhf-band.kicad_sch]
2026-02-02 Replaced AX5043 with AT86 for L Band in schematic
    [oresat-c3-sch-l-band.kicad_sch, oresat-c3-sch-uhf-band.kicad_sch]
2026-02-02 started routing UHF and L band chip replacement on PCB
    [oresat-c3-sch-l-band.kicad_sch, oresat-c3-sch-uhf-band.kicad_sch, oresat-c3.kicad_pcb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]
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2026-03-08 added mask on RF traces and fixed UHF power routing
    [oresat-c3.kicad_pcb]
2026-03-15 Design review on C3 v7.0
    Glenn and Andrew did a design review. Removed fiducials on back of board. Lots of schematic fixes, including
    direction connection of TCXOs to AT86s, corrected LPF of CLKO from AT86 to the synth reference, fixed drive
    levels both QPC switches in UHF radio, confirmed QPC directions, and some minor polishing.
    [oresat-c3-sch-connectors.kicad_sch, oresat-c3-sch-l-band.kicad_sch, oresat-c3-sch-opd-and-i2c.kicad_sch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]
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2026-03-17 Updating BOM and switching to oresat-passive footprints. Fixed some power cutoff limits, and fixed another DC voltage leverl on an LNA!
    [oresat-c3-sch-connectors.kicad_sch, oresat-c3-sch-l-band.kicad_sch, oresat-c3-sch-opd-and-i2c.kicad_sch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]
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2026-03-17 C3 v7.0 preliminarily done.
    Added SPARE7/SPARE8 GPIO for ESI, fixed all of the RF, re-did the BOM, polished as much as possible. Added Makefile and READMEs.
    [oresat-c3-sch-connectors.kicad_sch, oresat-c3-sch-l-band.kicad_sch, oresat-c3-sch-opd-and-i2c.kicad_sch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]
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2026-03-18 Fix a bunch of 3D models
    [oresat-c3.kicad_pcb]
2026-03-18 Last minute fixes.
    Added Theo's space buzzer. Added important kaomoji message. Fixed Makefile so that it ignores
    bad VRML footprints. Successfully builds!
    [oresat-c3-sch-connectors.kicad_sch, oresat-c3-sch-l-band.kicad_sch, oresat-c3-sch-osd3358-power.kicad_sch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]
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2026-03-19 Added L band ground cut (Glenn's fault). DRC errrors due to 50 ohm clearance; investigating custom rules now.
    [oresat-c3-sch-l-band.kicad_sch, oresat-c3-sch-osd3358-sd-emmc.kicad_sch, oresat-c3-sch-osd3358-sysboot.kicad_sch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]
2026-03-19 Fixed some RF DRC errors, and then added two custom rules to get rid of the pesky RF errors which leaves us with ZERO DRC errorsgit add .!
    [oresat-c3.kicad_pcb]
2026-03-20 Fixed custom design rules to handle RF traces, traces over unconnected pads in the eMMC, and copper by the SMPM connectors. Now does what we expect it to do. No DRC errors.
    [oresat-c3.kicad_pcb]
2026-03-21 Fixed a test point, cleaned up silk screen, and moved date up to today.
    [oresat-c3-sch-connectors.kicad_sch, oresat-c3-sch-l-band.kicad_sch, oresat-c3-sch-opd-and-i2c.kicad_sch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]
2026-03-22 Changed WDT tantalums to space-rated tantalums (fun) and fixed some BOM issues. Also possibly more silk screen cleanup.
    [oresat-c3-sch-l-band.kicad_sch, oresat-c3-sch-opd-and-i2c.kicad_sch, oresat-c3-sch-osd3358-usb-xtal.kicad_sch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]
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2026-04-07 Fix BOM errors given feedback from CM
    [oresat-c3-sch-connectors.kicad_sch, oresat-c3-sch-l-band.kicad_sch, oresat-c3-sch-uhf-band.kicad_sch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]
2026-04-10 Fixed BOM issue with eMMC
    [oresat-c3-sch-osd3358-sd-emmc.kicad_sch, oresat-c3.kicad_pcb]
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2026-04-21 Upgrade to KiCad 10, fix a few BOM entries, and we caught the first error! Go kicad 10.
    [oresat-c3-sch-connectors.kicad_sch, oresat-c3-sch-l-band.kicad_sch, oresat-c3-sch-opd-and-i2c.kicad_sch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]
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2026-06-10 Officially moving to C3 v7.1 with fixes based on the 7.0 and improvements from using the 7.0
    [oresat-c3-sch-connectors.kicad_sch, oresat-c3-sch-l-band.kicad_sch, oresat-c3-sch-opd-and-i2c.kicad_sch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]

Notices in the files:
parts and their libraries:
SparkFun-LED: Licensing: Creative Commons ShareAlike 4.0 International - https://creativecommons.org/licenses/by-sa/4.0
